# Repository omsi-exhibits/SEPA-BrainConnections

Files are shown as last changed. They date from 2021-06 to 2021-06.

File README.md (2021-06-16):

# OMSI's Brain Connections

## Next Steps
* update accelerometer code to use timers instead of delays
* update all the code to use timers instead of delays

## Other Todos
* consolodate notes
* write a good readme
* document High Level Design

## Known Bugs
none atm

# Flashing new firmware
The Itsybitsy32u4_5v is a litte finiky when it comes to flashing. The process that works most of the time for me is to double press the reset button
and then super quickly upload the code. Like within 300milliseconds or less. Maybe disabling serial.print()s would help? 

# Troubleshooting Tips
Removing and reinserting microcontroller is delicate and needs you to support the bottom of the mainboard with your hand.

## Fun Ideas
* Easter Egg Color pallette swap
* Sensor held on startup could change colors
* Handheld brain-connections game-thing

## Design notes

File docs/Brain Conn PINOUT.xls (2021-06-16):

Last updated: 11/30/20
LED Segment Names | SEGMENT LED COUNT | PINOUT FULL TABLE | Notes
node1LedCount | 24 | Digital out 7
node2LedCount | 24 | Digital out 7
node3LedCount | 24 | Digital out 7
node4LedCount | 24 | Digital out 7
node5LedCount | 24 | Digital out 7
node6LedCount | 24 | Digital out 7
node7LedCount | 24 | Digital out 7
conn1LedCount | 17 | Digital out 13
conn2LedCount | 8 | Digital out 13
conn3LedCount | 23 | Digital out 13
conn4LedCount | 23 | Digital out 13
conn5LedCount | 8 | Digital out 13
conn6LedCount | 17 | Digital out 13
conn7LedCount | 17 | Digital out 13
conn8LedCount | 10 | Digital out 13
conn9LedCount | 16 | Digital out 13
conn10LedCount | 21 | Digital out 13
conn11LedCount | 16 | Digital out 13
conn12LedCount | 16 | Digital out 13
orphan1LedCount | 15,5,3,5,15 | Digital out 5 | In code use the biggest orphan led count
orphan2LedCount | 11,12 | Digital out 5
orphan3LedCount | 7,10 | Digital out 5
orphans4LedCount | 19,7,2,7,19 | Digital out 5
orphans5LedCount | 10,7 | Digital out 5
orphans6LedCount | 11,11 no output wire | Digital out 5
sensor Status LEDs | 8 | Digital out 14
TILT_sensor | /ADXL343 accel | SPI wire buss
node1Sensor |  | ANALOG pin 0
node2Sensor |  | ANALOG pin 1
node3Sensor |  | ANALOG pin 2
node4Sensor |  | ANALOG pin 3
node5Sensor |  | ANALOG pin 4
node6Sensor |  | ANALOG pin 5
node7Sensor |  | ANALOG pin 6
Audio_1 | (IDLE sound - hold HIGH for looping) | DIGITAL out 12
Audio_2 | (Connection sound, edge triggered) | DIGITAL out 11
Audio_3 | (Node Sound, edge triggered) | DIGITAL out 10
Audio_4 | (Win Song, edge triggered) | DIGITAL out 9
Audio_5 | (Start song, edge triggered) | DIGITAL out 8

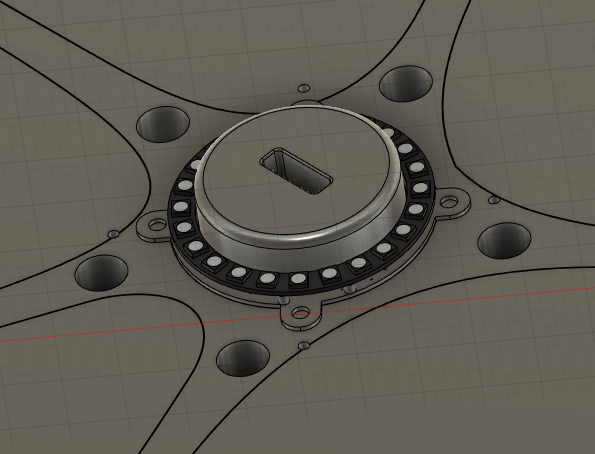
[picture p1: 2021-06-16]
3D/Brain Conn 3D Assets 7-22-20/LED Ring Location.png

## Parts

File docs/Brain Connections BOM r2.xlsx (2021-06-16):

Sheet: Summary Page
Estimate |  |  |  |  | DGTL.
Project Name | Brain Connections |  | Client | OMSI
Project # |  |  | Client Name | Caty Headskog
Date | 2020-03-23 |  | Launch Date | TBD
Production |  | PRICING | NOTES
Hardware |  | $802.88 | Please see BOM tab for detail. (Supplied by OMSI)
Total |  | $802.88

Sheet: BOM
Project Name | Brain Connections | Delivery Date | TBD
Project # | 0 | Ship Date | TBD
ITEM | DESCRIPTION | QTY | UNIT PRICE | SUBTOTAL | Notes
Opto Sensors | OPB732 | 7 | $4.04 | $28.28 | https://www.digikey.com/short/zjwwc4
Neopixel strip | 60/meter RGBW sk6812 (5050) (4 meter roll) | 2 | $107.80 | $215.60 | https://www.mouser.com/ProductDetail/Adafruit/2842
NeoPixel Rings | 24 pixels, RGBW | 7 | $19.95 | $139.65 | https://www.digikey.com/short/zjvqdr
3 axis accelerometer | adxl 343 | 1 | $5.95 | $5.95 | https://www.digikey.com/short/zjwwjd
Microcontroller | itsybitsy 32u4 5v 16mhz | 1 | $9.95 | $9.95 | https://www.digikey.com/short/zjwf45
12v power supply | 240w 115vac to 12vdc supply | 1 | $78.14 | $78.14 | https://www.digikey.com/short/zjwdpc
Dc - dc converter | 55w 12vdc to 5vdc converter | 3 | $16.41 | $49.23 | https://www.digikey.com/short/zjwd54
JST-SH with 3 leads extensions | 3 pin male + female set at 10 pair x 0.5 meter | 1 | $14.39 | $14.39 | https://www.amazon.com/RGBZONE-Extension-solderless-Connector-Symphony/dp/B06XSDZLPC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
JST-SH with 3 leads | 3 pin male + female set at 50 pair | 1 | $10.99 | $10.99 | https://www.amazon.com/HKBAYI-50Pair-50sets-Connector-WS2812B/dp/B00NBSH4CA
Phoenix connectors | TERM BLOCK PLUG 2POS STR 5.08MM | 14 | $3.20 | $44.80 | https://www.digikey.com/short/zjd0pv
Phoenix connectors | TERM BLOCK PLUG 3POS STR 5.08MM | 18 | $4.80 | $86.40 | https://www.digikey.com/short/zjd0zj
Phoenix connectors | TERM BLOCK PLUG 4POS STR 5.08MM | 2 | $6.44 | $12.88 | https://www.digikey.com/short/zjd0z2
Phoenix connectors | TERM BLOCK HDR 2POS 90DEG 5.08MM | 14 | $0.64 | $8.96 | https://www.digikey.com/short/zjd078
Phoenix connectors | TERM BLOCK HDR 3POS 90DEG 5.08MM | 18 | $1.03 | $18.54 | https://www.digikey.com/short/zjd032
Phoenix connectors | TERM BLOCK HDR 4POS 90DEG 5.08MM | 2 | $1.40 | $2.80 | https://www.digikey.com/short/zjd03d
Phoenix connectors | TERM BLK 6P SIDE ENT 5.08MM PCB | 1 | $3.16 | $3.16 | https://www.digikey.com/short/zjd00v
Panasonic Capacitors | CAP ALUM 1000UF 20% 25V RADIAL | 4 | $0.79 | $3.16 | https://www.digikey.com/short/zjv8j5
100 Ohm 1/4 watt resistor | RES 100 OHM 1/4W 5% AXIAL | 7 | $0.10 | $0.70 | https://www.digikey.com/short/zjv8b2
330 Ohm 1/4 watt resistor | RES 330 OHM 1/4W 5% AXIAL | 4 | $0.10 | $0.40 | https://www.digikey.com/short/zjv8h1
1k Ohm 1/4 watt resistor | RES 1K OHM 1/4W 5% AXIAL | 7 | $0.10 | $0.70 | https://www.digikey.com/short/zjv8b4
aluminum track | 0.69in w x 0.28in high OD (0.48" wide ID) | 1 | $68.20 | $68.20 | https://www.amazon.com/hunhun-Aluminum-Mounting-Installations-Installation/dp/B07F923CXW
audio interface | Wav Trigger WIG-13660 | 1 | $0.00 | $0.00 | Provided by OMSI
amplifier |  | 1 | $0.00 | $0.00 | Provided by OMSI
 |  |  |  | $802.88

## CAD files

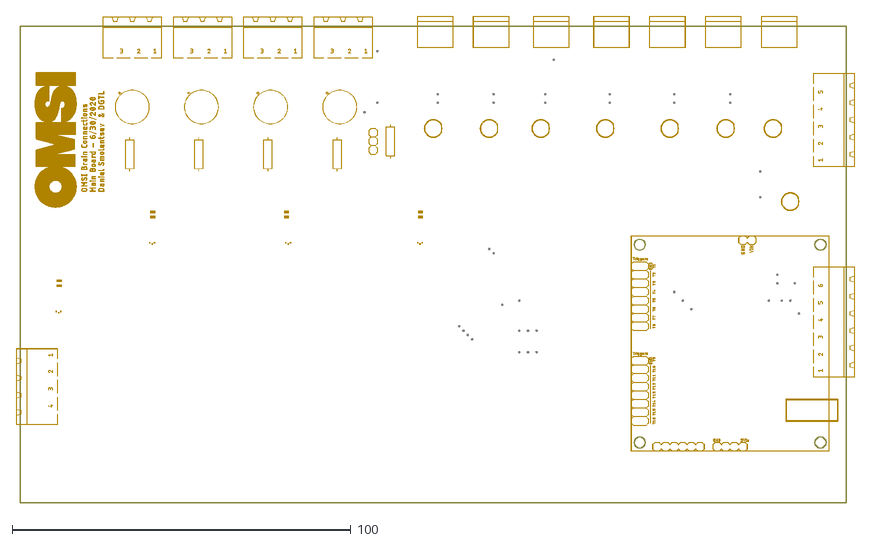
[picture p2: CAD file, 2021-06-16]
3D/Brain Conn 3D Assets 7-22-20/Mainboard - OMSI_TABLE_R12_v4 - Simple.dxf
247.5 x 143.6

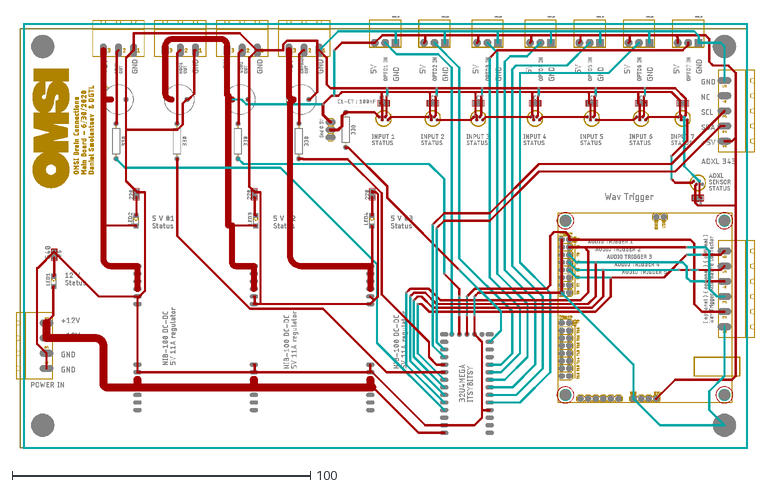
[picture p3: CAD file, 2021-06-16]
3D/Brain Conn 3D Assets 7-22-20/alt files/Mainboard - OMSI_TABLE_R12_v4 - Complex.dxf
247.5 x 145.0

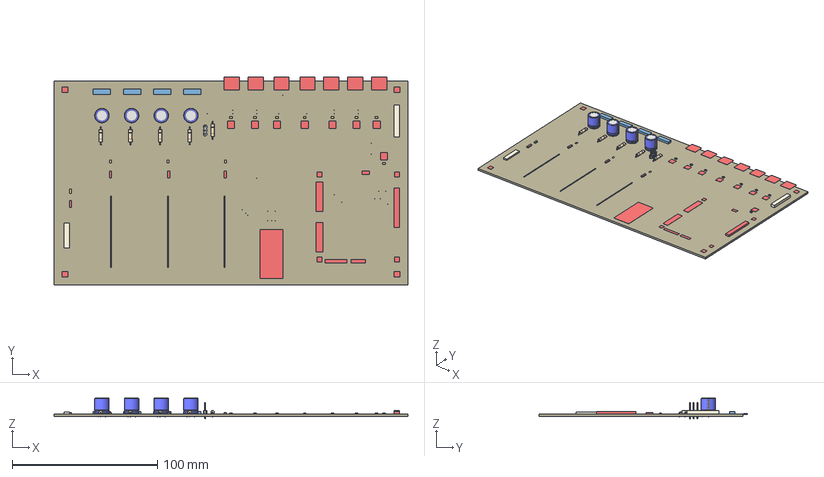
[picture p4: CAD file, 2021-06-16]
3D/Brain Conn 3D Assets 7-22-20/alt files/Mainboard - OMSI_TABLE_R12_v4.step
243.8 x 143.5 x 14.3 mm
Board
MSTBA3 x 4
CHIPLED_1206 x 4
MEANWELL_NID100 x 3
ITSYBITSY_32U4
C-POL-US_RADIAL-11MM-DIA x 4
MSTBA4
MSTBA5
STANDOFF_ELECTRICAL5-32 x 4
1X06
STAND-OFF x 4
M08X2 x 2
1X04
M02PTH
CONN_03 x 7
APA106-F5 x 8
100nF x 8
MSTBA6
1X03

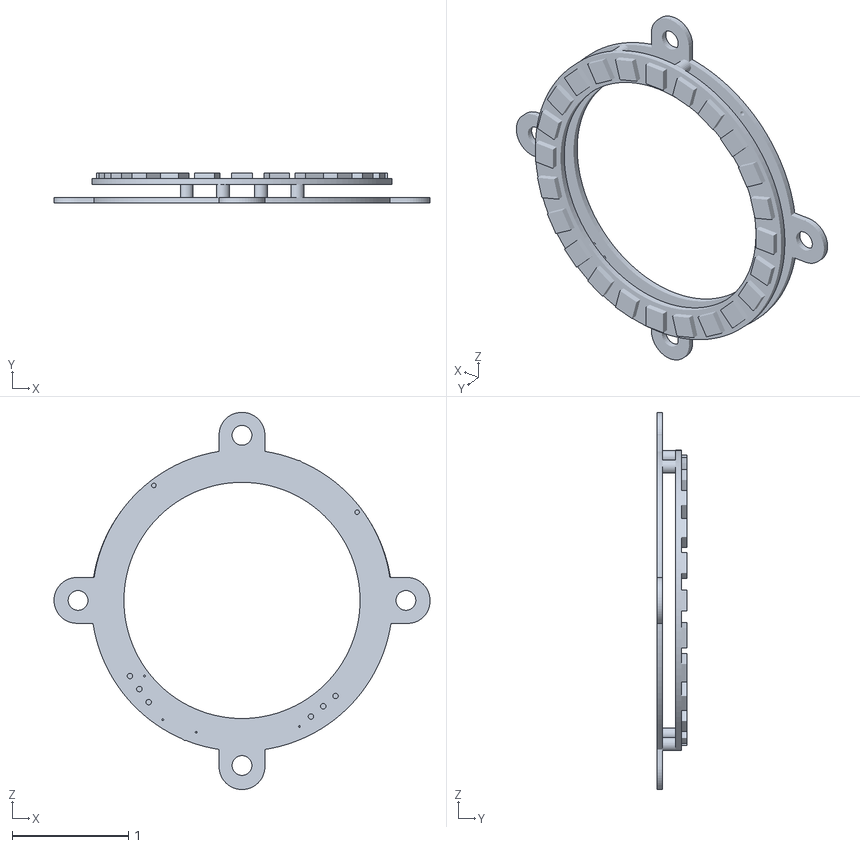
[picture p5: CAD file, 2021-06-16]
3D/Brain Conn 3D Assets 7-22-20/LED Ring - LED ASSEMBLY.stl
3.23 x 0.26 x 3.24

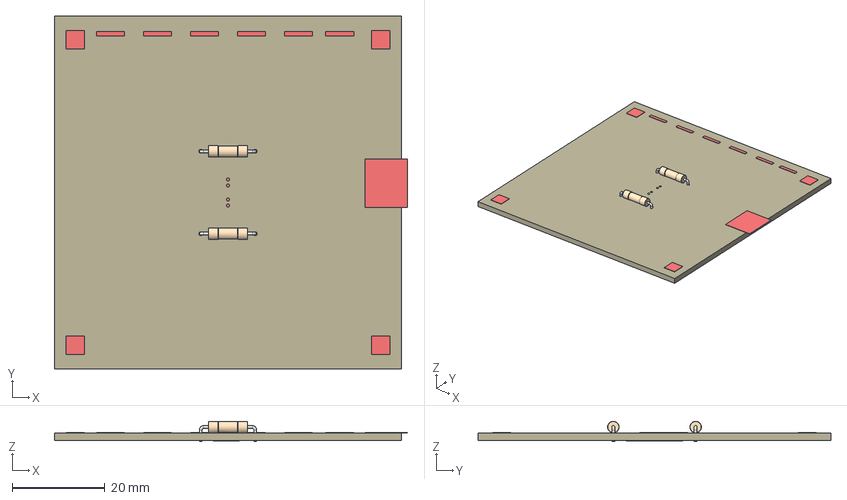
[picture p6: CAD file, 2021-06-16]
3D/Brain Conn 3D Assets 7-22-20/alt files/Sensorboard - Ring_opto_interface_v3.step
76.2 x 76.2 x 4.42 mm
Board
1X03-CLEANBIG x 6
10k x 2
STANDOFF_ELECTRICAL5-32 x 4
OPB732
CONN_03

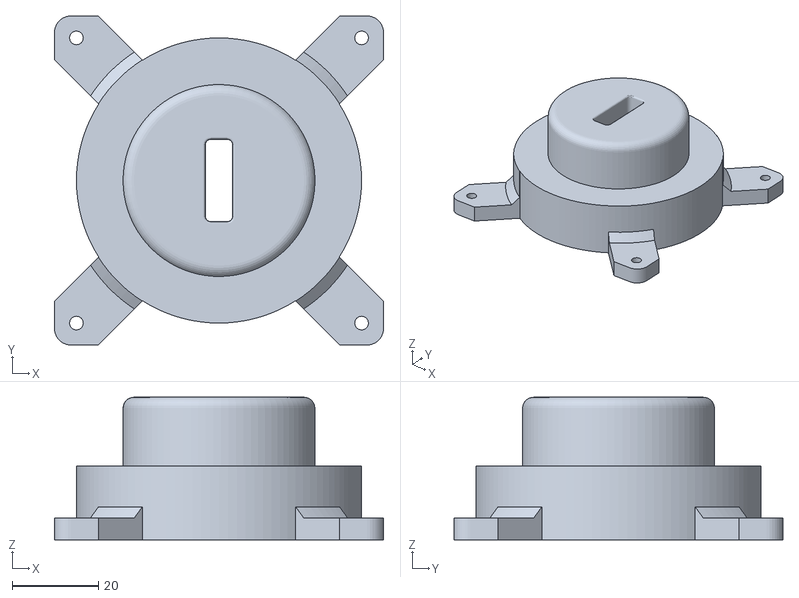
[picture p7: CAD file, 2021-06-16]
3D/Spacer 4 Holes.stl
76.2 x 76.2 x 33.0

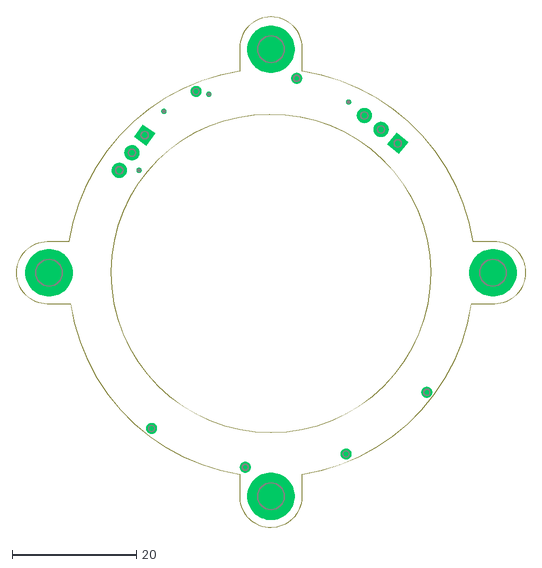
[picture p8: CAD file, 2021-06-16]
pcb/eagle/neopixel_ring_24_holder/Adafruit NeoPixel Ring 24 B - Holder 3 Outline.dxf
82.1 x 82.3

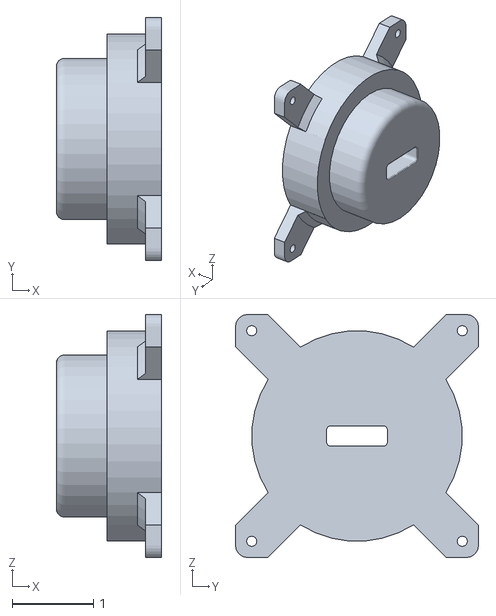
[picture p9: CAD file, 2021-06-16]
3D/3D Spacer v2.obj
1.30 x 3.00 x 3.00

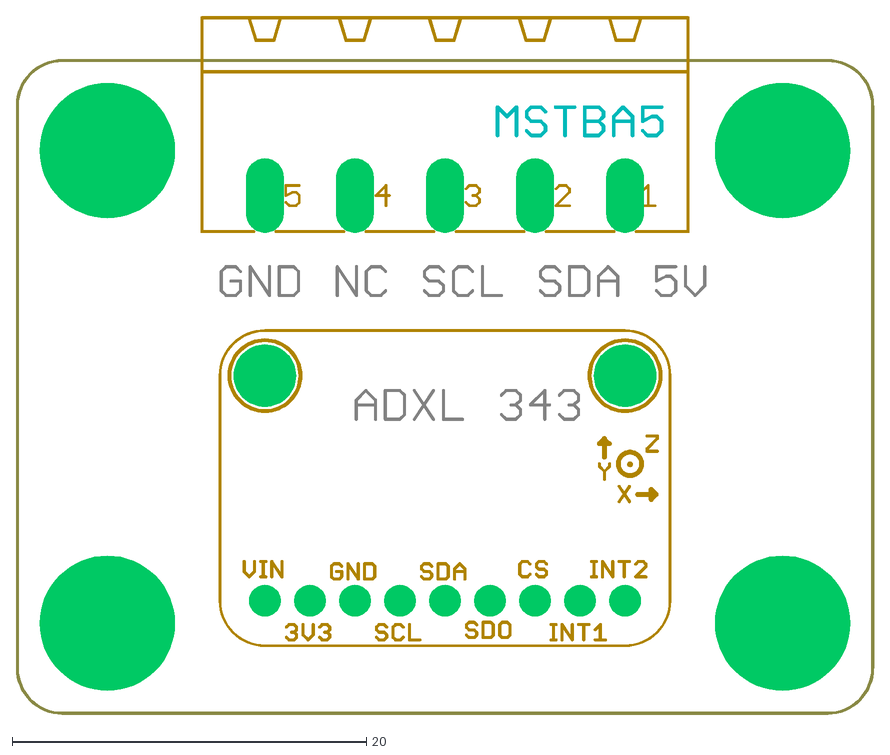
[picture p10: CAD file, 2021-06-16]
pcb/eagle/pcb updates redesign/ADXL Breakout Board V1.dxf
48.4 x 39.4

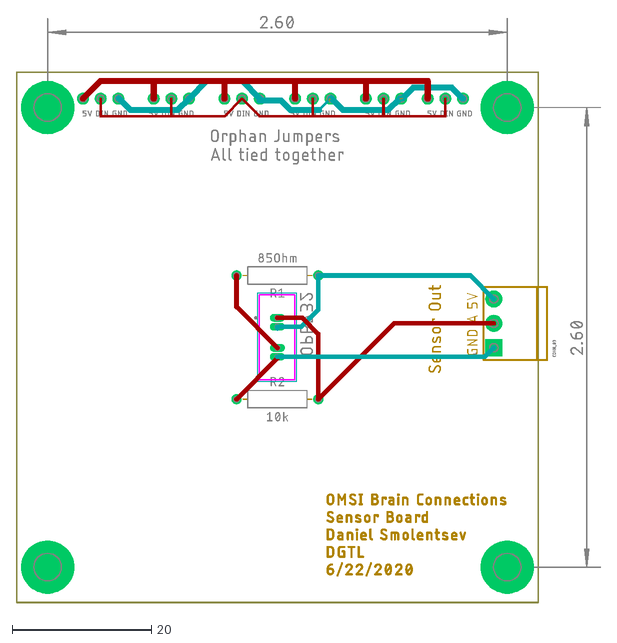
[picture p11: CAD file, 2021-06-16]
3D/Brain Conn 3D Assets 7-22-20/Sensor board - Ring_opto_interface_v3.dxf
84.0 x 84.3

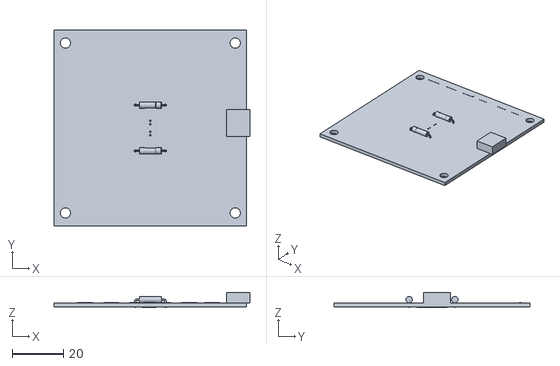
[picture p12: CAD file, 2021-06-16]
3D/Brain Conn 3D Assets 7-22-20/Sensor Board - Ring_opto_interface_v3 v2.stl
76.2 x 76.2 x 6.02

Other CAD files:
3D/Brain Conn 3D Assets 7-22-20/MainBoard - OMSI_TABLE_R12_v4.stl
3D/3D Spacer v2.dxf
3D/3D Spacer v2.f3d
3D/Brain Conn 3D Assets 7-22-20/Accelerometer - ADXL Breakout Board V1 v1.stl
3D/OMSI_TABLE_STATLEDS.f3z
3D/Ring_OPTO_2V5.f3z
3D/node spacer v2.f3d

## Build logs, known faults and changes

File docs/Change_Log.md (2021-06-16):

# Brain Connections Change log

5/14/20 Expanded the number of nodes, connections, orphans
Removed Words
5/20/20
mcu is running out of RAM. 
5/21/20
To reduce RAM usage I replaced the Adafruit Accelerometer library with sparkfun one.
There is still not enough space in SRAM. Converted the Serial Prints
to use F() to wrap strings to make it save into program memory instead of RAM.
Those two changes yielded enough space in SRAM.
5/21/20
Updated the Opto input pins to match the PCBs out of order pins.
5/26/20
Fixing connection segment bugs.
Added a Serial input from computer to trigger Nodes.
6/3/20
Added Individual OPTOtriggerValue for each OPTO
6/24/20 update
Wav trigger audio inputs set to these pins
const int Audio_1 = 8; // Idle Song - hold level high to loop
const int Audio_2 = 9; // Connection on 10 - edge triggered
const int Audio_3 = 10; // Node sound on 9 - edge triggered
const int Audio_4 = 11; // Win sound on 8 - edge triggered
const int Audio_5 = 12; // Start Song on 11 - edge triggered
7/15/20
Modified led type for sensorsout to neopixel GRB
Updated Sensor pins
Updated Audio out pins
11-23-20
Updated sensor trigger values to 350 on line#s105
4-14-21
Fixed Audio trigger pins to play win sound correctly
6-15-21
Updated accelZTriggerValue from 20 to 11 for a more responsive trigger
Fixed Node7 not dimming

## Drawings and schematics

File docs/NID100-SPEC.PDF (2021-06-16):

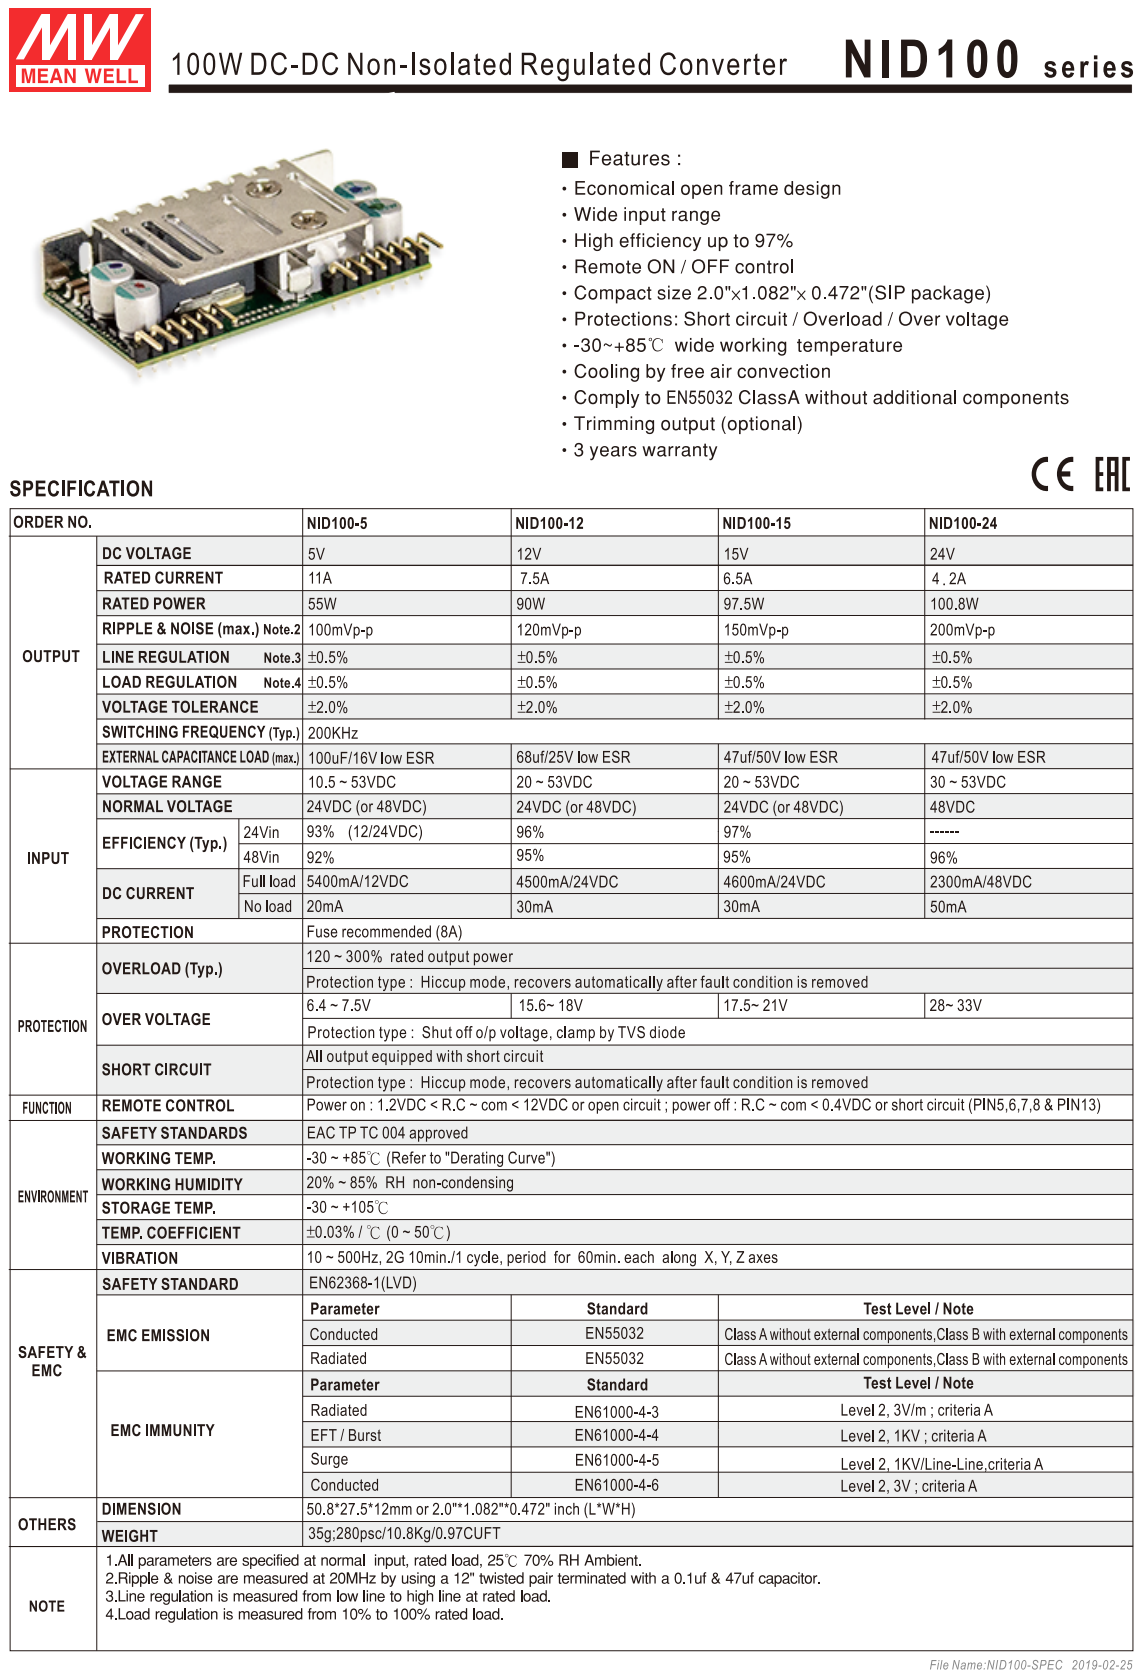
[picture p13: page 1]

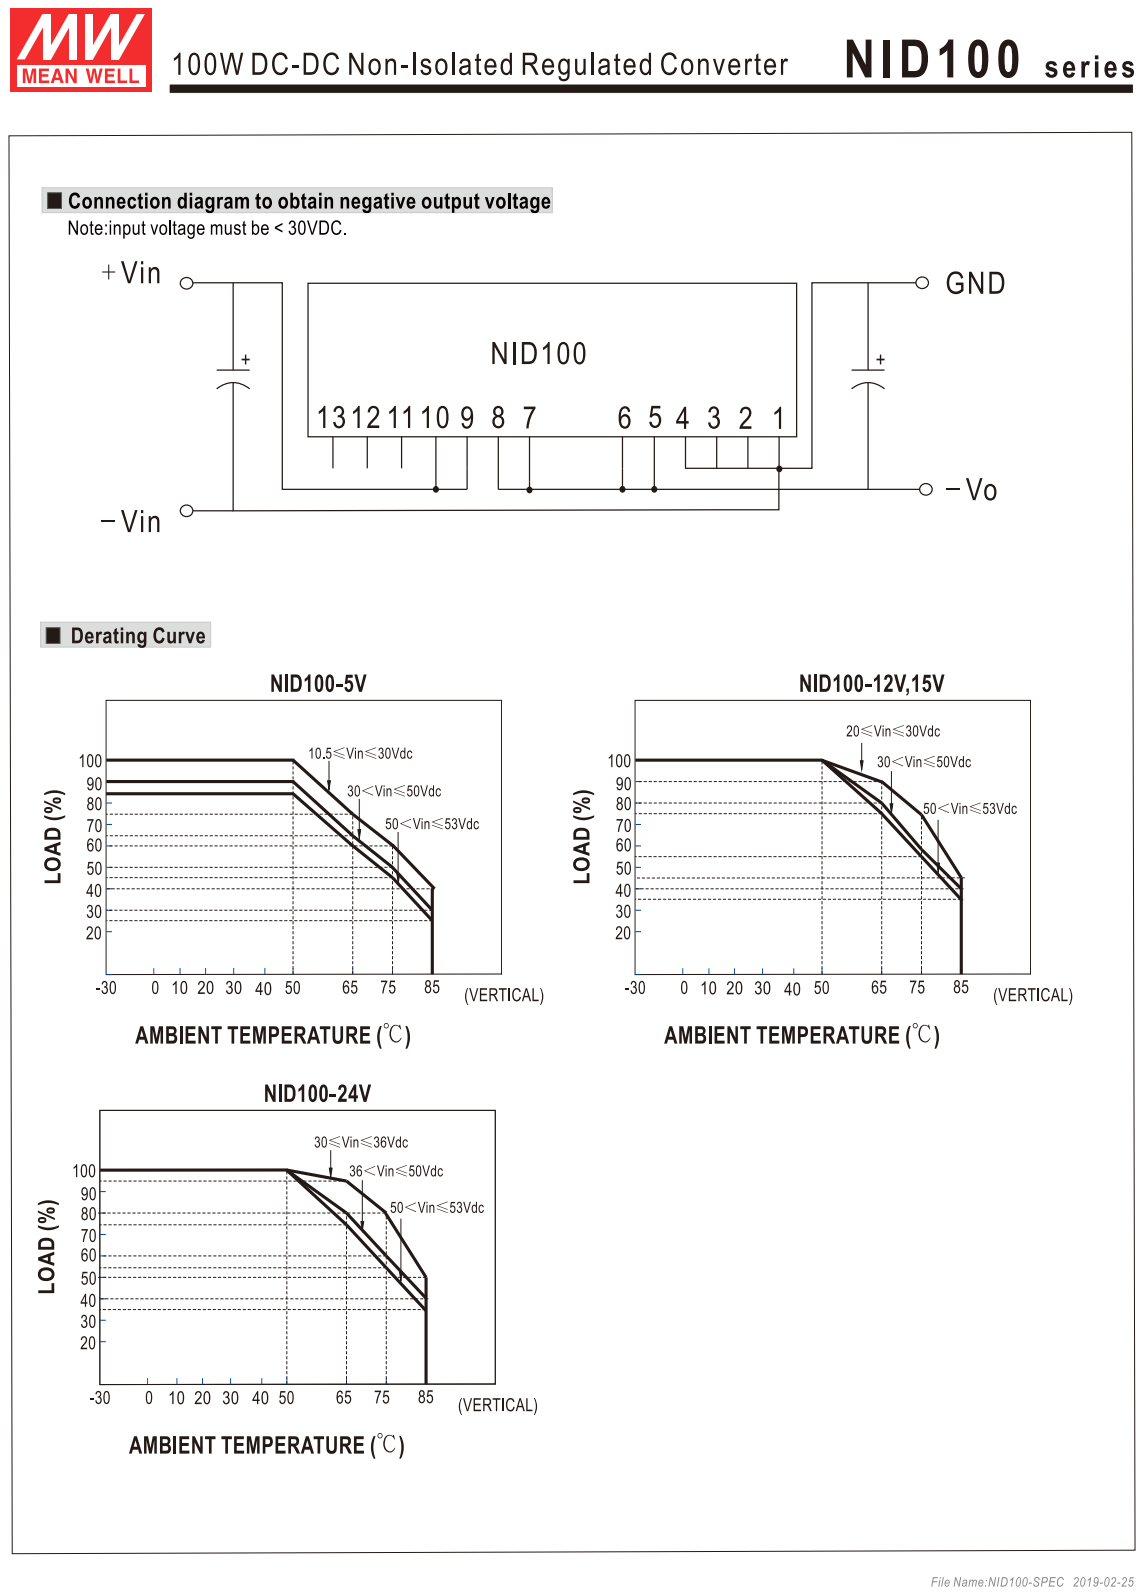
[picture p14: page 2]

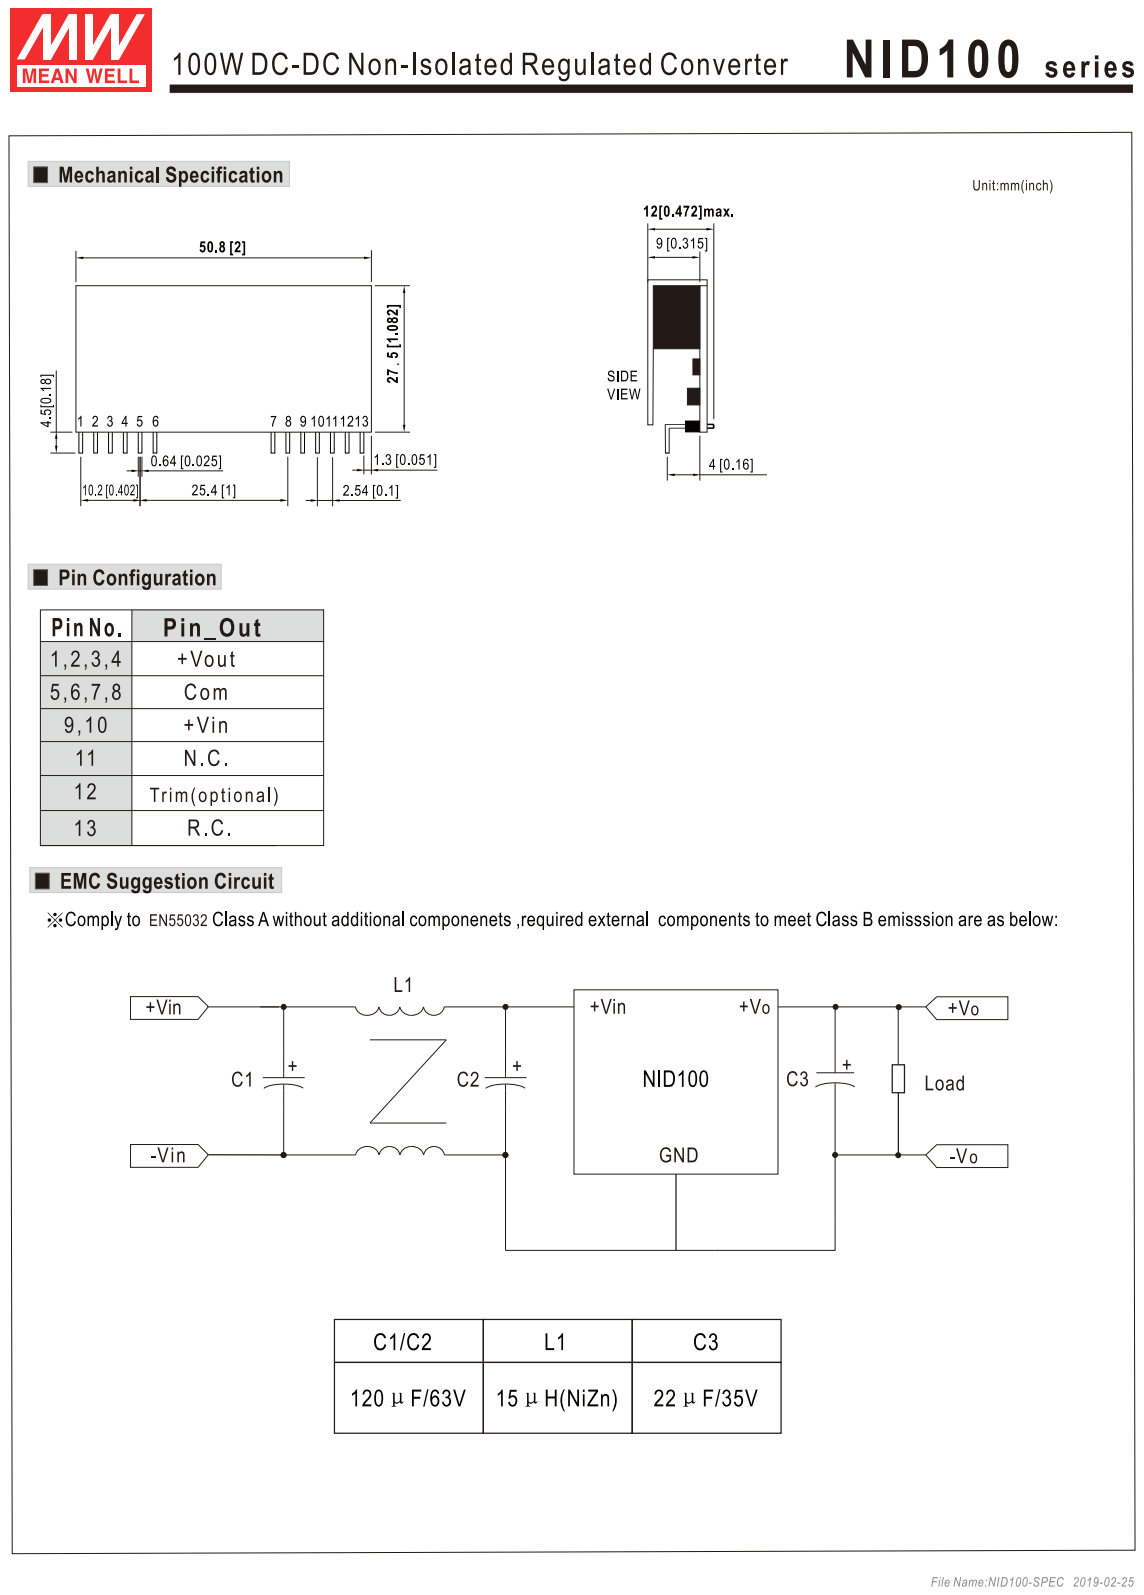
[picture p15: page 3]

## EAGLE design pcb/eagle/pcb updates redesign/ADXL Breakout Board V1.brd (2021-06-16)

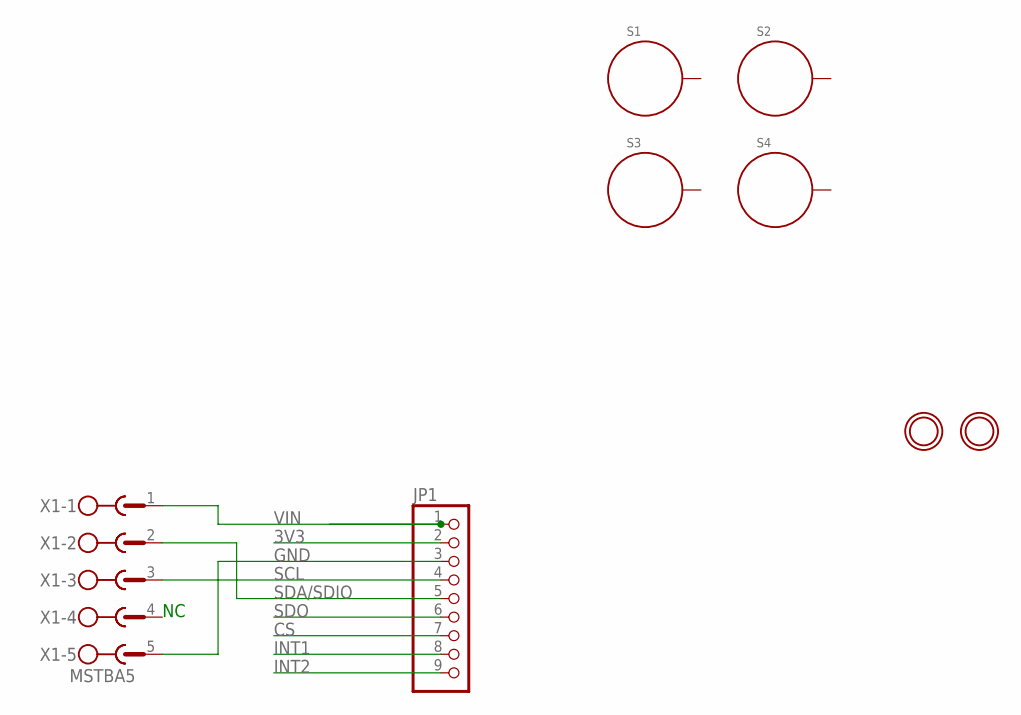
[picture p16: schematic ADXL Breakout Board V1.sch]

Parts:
JP1: HEADER-1X970MIL; 1X09_ROUND_70
S1, S2, S3, S4: STANDOFF_ELECTRICAL5-32; STANDOFF_ELECTRICAL_5_32
U$4, U$6: MOUNTINGHOLE2.5; MOUNTINGHOLE_2.5_PLATED
X1: MSTBA5

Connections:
3V3: JP1.2
CS: JP1.7
GND: JP1.3, X1.5
INT1: JP1.8
INT2: JP1.9
SCL: JP1.4, X1.3
SDA/SDIO: JP1.5, X1.2
SDO: JP1.6
VIN: JP1.1, X1.1

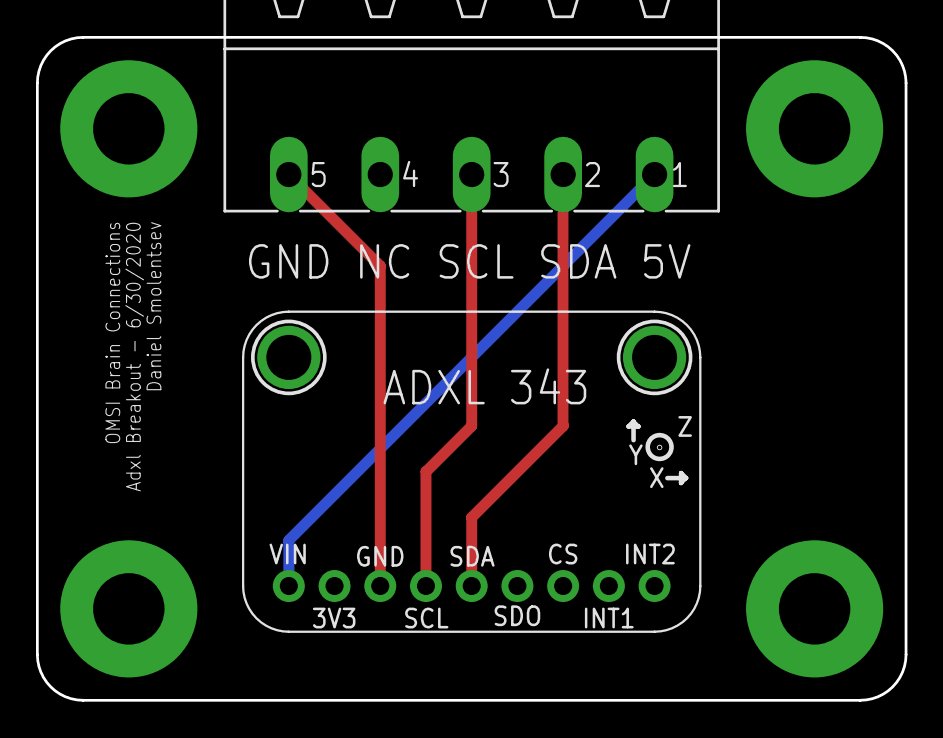
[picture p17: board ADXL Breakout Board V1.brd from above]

Board: 2 copper layers, 48.3 x 36.8 mm, 8 parts (0 on the bottom side), 4 nets.

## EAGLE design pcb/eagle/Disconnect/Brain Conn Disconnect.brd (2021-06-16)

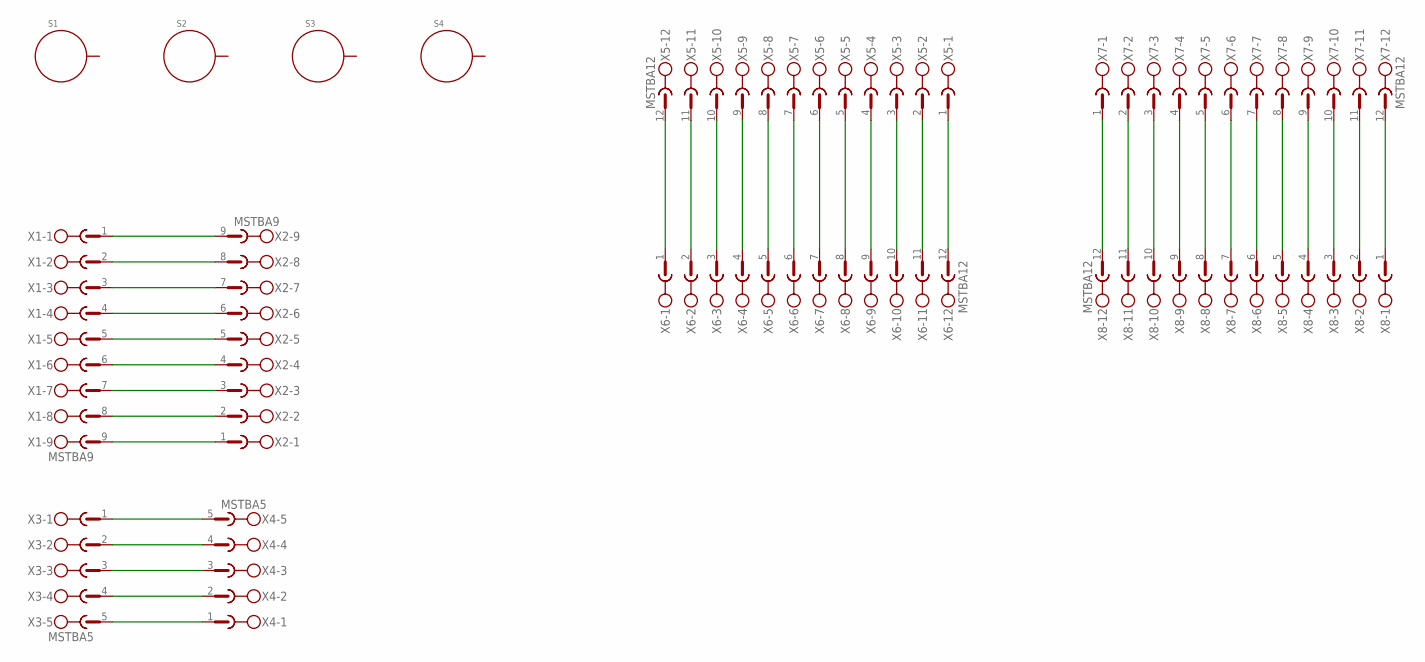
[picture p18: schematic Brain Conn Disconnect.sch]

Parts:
S1, S2, S3, S4: STANDOFF_ELECTRICAL144; STANDOFF_ELECTRICAL_144MILL_NORMAL_SCREW
X1, X2: MSTBA9
X3, X4: MSTBA5
X5, X6, X7, X8: MSTBA12

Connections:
unnamed: X3.1, X4.5
unnamed: X3.2, X4.4
unnamed: X3.3, X4.3
unnamed: X3.4, X4.2
unnamed: X3.5, X4.1
unnamed: X1.1, X2.9
unnamed: X1.2, X2.8
unnamed: X1.3, X2.7
unnamed: X1.4, X2.6
unnamed: X1.5, X2.5
unnamed: X1.6, X2.4
unnamed: X1.7, X2.3
unnamed: X1.8, X2.2
unnamed: X1.9, X2.1
unnamed: X5.12, X6.1
unnamed: X5.11, X6.2
unnamed: X5.10, X6.3
unnamed: X5.9, X6.4
unnamed: X5.8, X6.5
unnamed: X5.7, X6.6
unnamed: X5.6, X6.7
unnamed: X5.5, X6.8
unnamed: X5.4, X6.9
unnamed: X5.3, X6.10
unnamed: X5.2, X6.11
unnamed: X5.1, X6.12
unnamed: X7.1, X8.12
unnamed: X7.2, X8.11
unnamed: X7.3, X8.10
unnamed: X7.4, X8.9
unnamed: X7.5, X8.8
unnamed: X7.6, X8.7
unnamed: X7.7, X8.6
unnamed: X7.8, X8.5
unnamed: X7.9, X8.4
unnamed: X7.10, X8.3
unnamed: X7.11, X8.2
unnamed: X7.12, X8.1

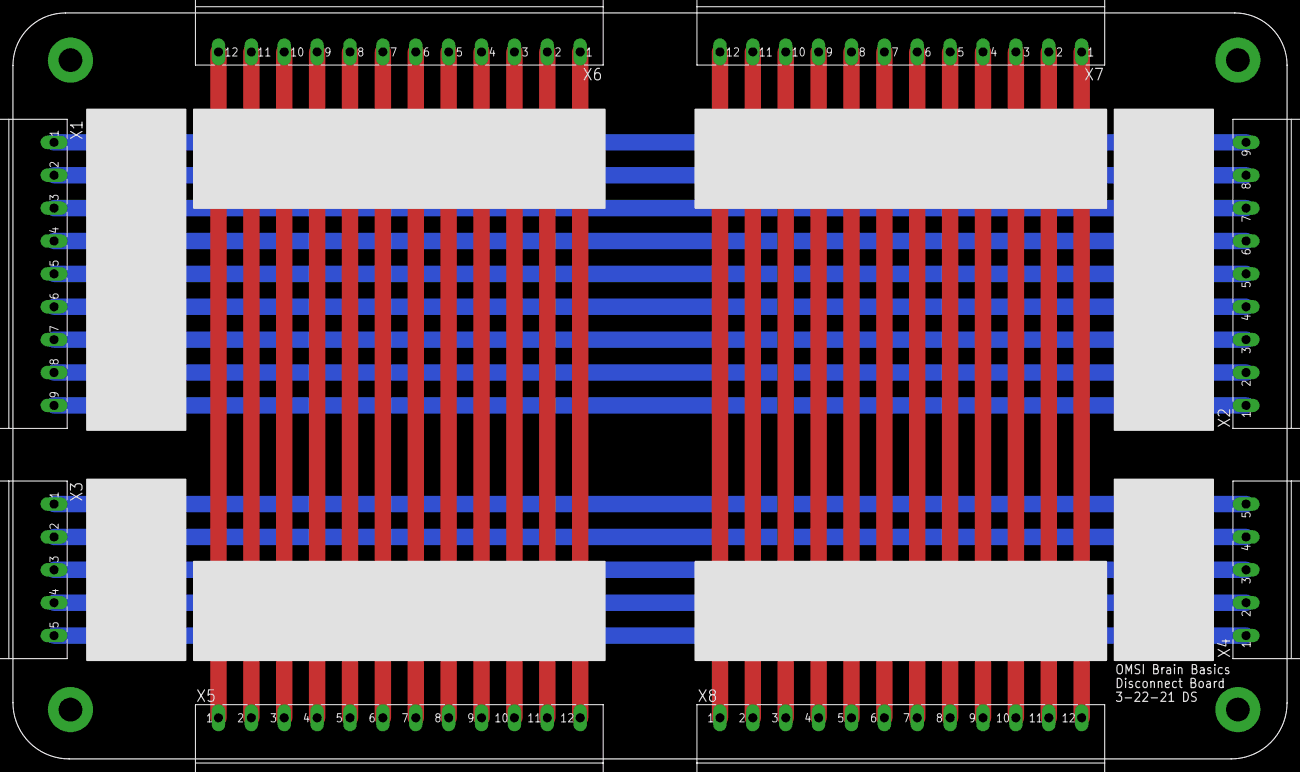
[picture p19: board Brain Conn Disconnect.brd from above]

Board: 2 copper layers, 196.8 x 115.2 mm, 12 parts (0 on the bottom side), 38 nets.

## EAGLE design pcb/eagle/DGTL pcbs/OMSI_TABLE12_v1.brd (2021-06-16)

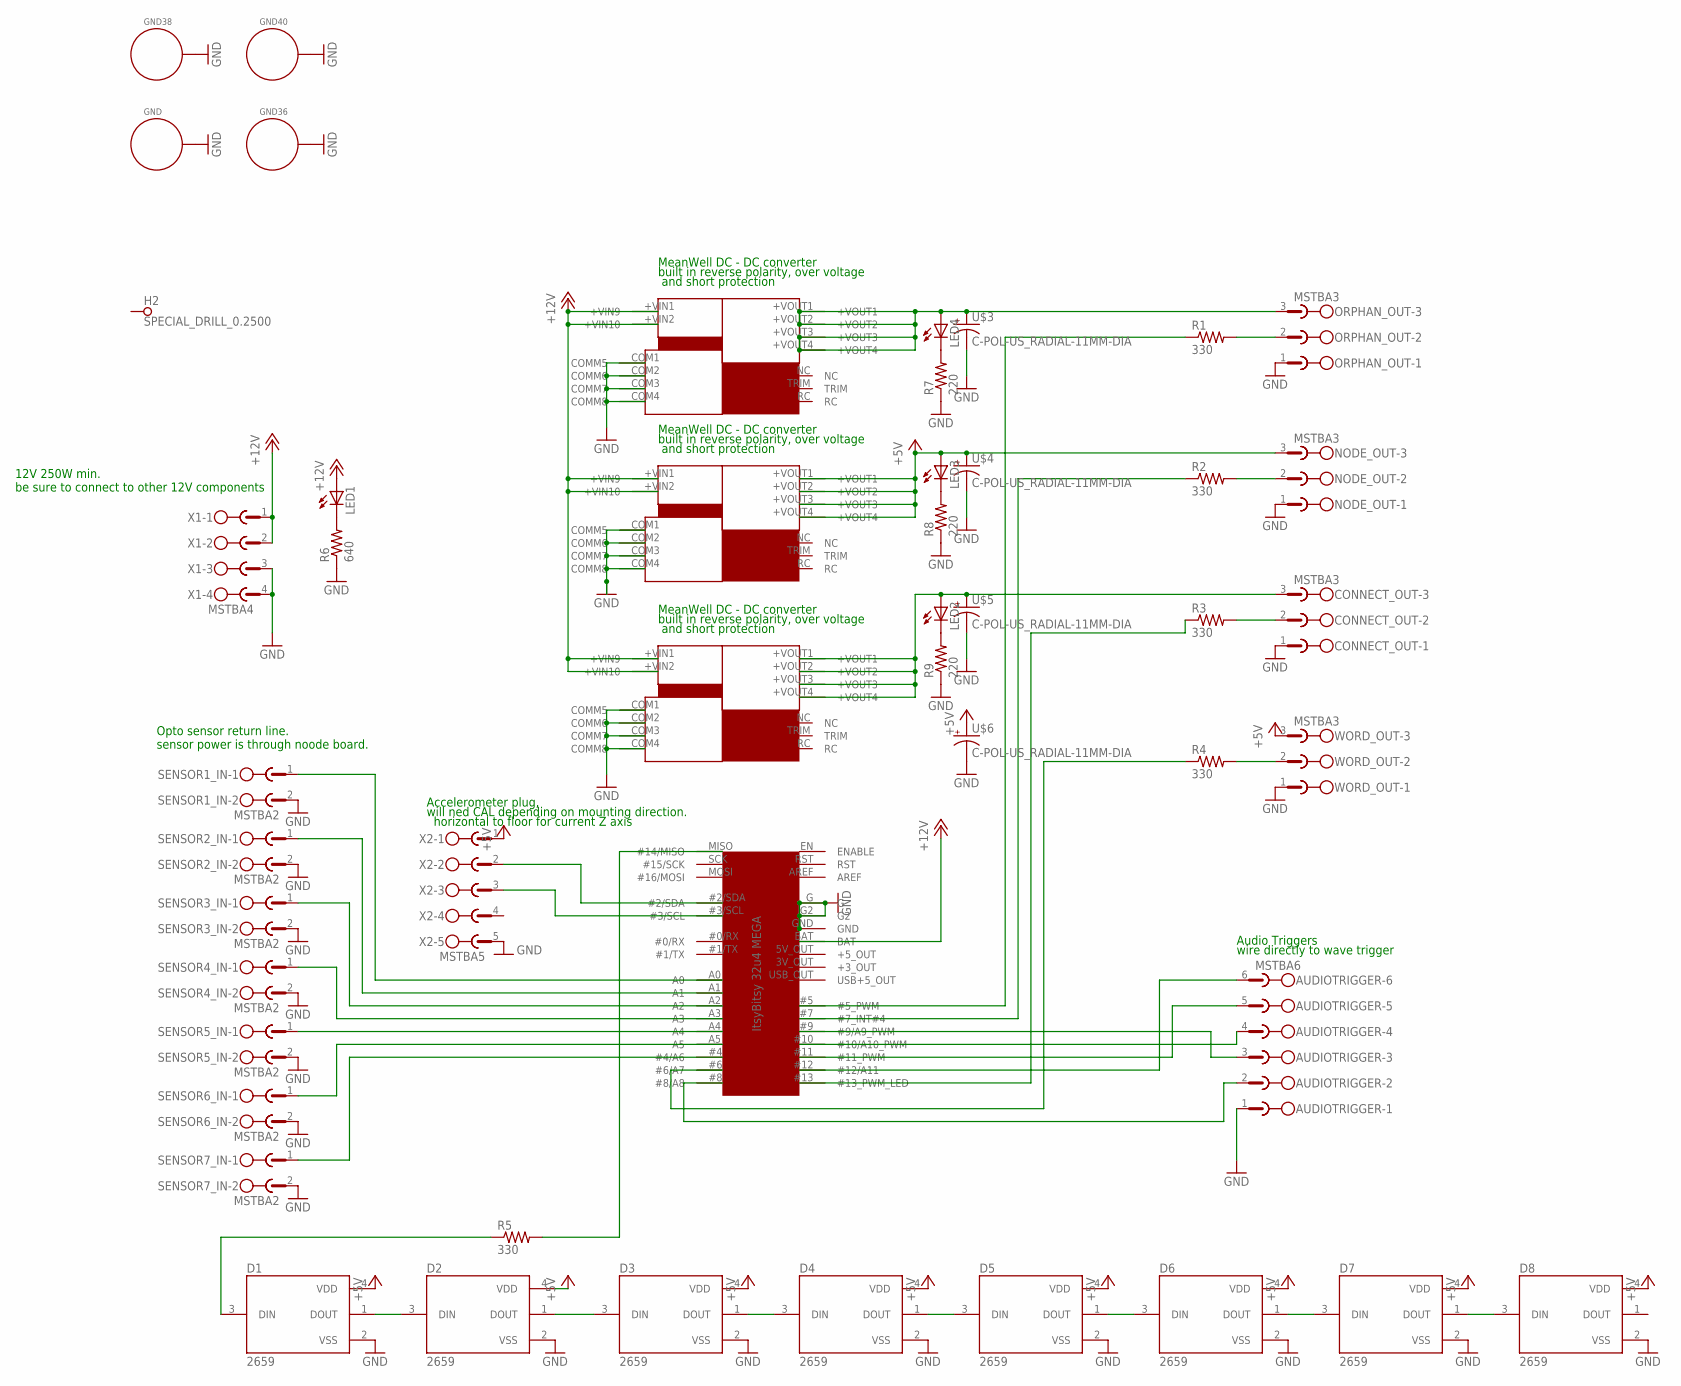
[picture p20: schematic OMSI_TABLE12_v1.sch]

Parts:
AUDIOTRIGGER: MSTBA6
CONNECT_OUT: MSTBA3
D1, D2, D3, D4, D5, D6, D7, D8: 2659
GND, GND36, GND38, GND40: STANDOFF_ELECTRICAL5-32; STANDOFF_ELECTRICAL_5_32
H2: SPECIAL_DRILL_0.2500; PAD_0.2500
LED1, LED2, LED3, LED4: LEDCHIPLED_1206; CHIPLED_1206
MEANWELL_NID100_1, MEANWELL_NID100_2, MEANWELL_NID100_3: MEANWELL_NID100
NODE_OUT: MSTBA3
ORPHAN_OUT: MSTBA3
R1, R2, R3, R4, R5: 330; RESAD1176W63L850D250B
R6: 640; R0805
R7, R8, R9: 220; R0805
SENSOR1_IN, SENSOR2_IN, SENSOR3_IN, SENSOR4_IN, SENSOR5_IN, SENSOR6_IN, SENSOR7_IN: MSTBA2
U$1: ITSYBITSY_32U4
U$3, U$4, U$5, U$6: C-POL-US_RADIAL-11MM-DIA; CAPPRD508W65D1000H1100B
WORD_OUT: MSTBA3
X1: MSTBA4
X2: MSTBA5

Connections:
+3_OUT: U$1.3V_OUT (+3_OUT)
+5V: D1.4 (VDD), D2.4 (VDD), D3.4 (VDD), D4.4 (VDD), D5.4 (VDD), D6.4 (VDD), D7.4 (VDD), D8.4 (VDD), LED3.A, MEANWELL_NID100_3.+VOUT1, MEANWELL_NID100_3.+VOUT2, MEANWELL_NID100_3.+VOUT3, MEANWELL_NID100_3.+VOUT4, NODE_OUT.3, U$4.1 (+), U$6.1 (+), WORD_OUT.3, X2.1
+5_OUT: U$1.5V_OUT (+5_OUT)
+12V: LED1.A, MEANWELL_NID100_1.+VIN1 (+VIN9), MEANWELL_NID100_1.+VIN2 (+VIN10), MEANWELL_NID100_2.+VIN1 (+VIN9), MEANWELL_NID100_2.+VIN2 (+VIN10), MEANWELL_NID100_3.+VIN1 (+VIN9), MEANWELL_NID100_3.+VIN2 (+VIN10), U$1.BAT, X1.1, X1.2
AREF: U$1.AREF
GND: AUDIOTRIGGER.1, CONNECT_OUT.1, D1.2 (VSS), D2.2 (VSS), D3.2 (VSS), D4.2 (VSS), D5.2 (VSS), D6.2 (VSS), D7.2 (VSS), D8.2 (VSS), GND.P1, GND36.P1, GND38.P1, GND40.P1, MEANWELL_NID100_1.COM1 (COMM5), MEANWELL_NID100_1.COM2 (COMM6), MEANWELL_NID100_1.COM3 (COMM7), MEANWELL_NID100_1.COM4 (COMM8), MEANWELL_NID100_2.COM1 (COMM5), MEANWELL_NID100_2.COM2 (COMM6), MEANWELL_NID100_2.COM3 (COMM7), MEANWELL_NID100_2.COM4 (COMM8), MEANWELL_NID100_3.COM1 (COMM5), MEANWELL_NID100_3.COM2 (COMM6), MEANWELL_NID100_3.COM3 (COMM7), MEANWELL_NID100_3.COM4 (COMM8), NODE_OUT.1, ORPHAN_OUT.1, R6.1, R7.1, R8.1, R9.1, SENSOR1_IN.2, SENSOR2_IN.2, SENSOR3_IN.2, SENSOR4_IN.2, SENSOR5_IN.2, SENSOR6_IN.2, SENSOR7_IN.2, U$1.G, U$1.G2, U$1.GND, U$3.2 (-), U$4.2 (-), U$5.2 (-), U$6.2 (-), WORD_OUT.1, X1.3, X1.4, X2.5
unnamed: LED4.A, MEANWELL_NID100_2.+VOUT1, MEANWELL_NID100_2.+VOUT2, MEANWELL_NID100_2.+VOUT3, MEANWELL_NID100_2.+VOUT4, ORPHAN_OUT.3, U$3.1 (+)
unnamed: U$1.#2/SDA, X2.2
unnamed: U$1.#3/SCL, X2.3
unnamed: SENSOR1_IN.1, U$1.A0
unnamed: SENSOR2_IN.1, U$1.A1
unnamed: SENSOR3_IN.1, U$1.A2
unnamed: CONNECT_OUT.3, LED2.A, MEANWELL_NID100_1.+VOUT1, MEANWELL_NID100_1.+VOUT2, MEANWELL_NID100_1.+VOUT3, MEANWELL_NID100_1.+VOUT4, U$5.1 (+)
unnamed: SENSOR4_IN.1, U$1.A3
unnamed: ORPHAN_OUT.2, R1.2
unnamed: R1.1, U$1.#5 (#5_PWM)
unnamed: NODE_OUT.2, R2.2
unnamed: SENSOR5_IN.1, U$1.A4
unnamed: SENSOR6_IN.1, U$1.A5
unnamed: SENSOR7_IN.1, U$1.#4 (#4/A6)
unnamed: R2.1, U$1.#7 (#7_INT#4)
unnamed: CONNECT_OUT.2, R3.2
unnamed: R3.1, U$1.#13 (#13_PWM_LED)
unnamed: R4.2, WORD_OUT.2
unnamed: R4.1, U$1.#6 (#6/A7)
unnamed: AUDIOTRIGGER.6, U$1.#12 (#12/A11)
unnamed: AUDIOTRIGGER.5, U$1.#11 (#11_PWM)
unnamed: R5.2, U$1.MISO (#14/MISO)
unnamed: AUDIOTRIGGER.4, U$1.#10 (#10/A10_PWM)
unnamed: AUDIOTRIGGER.3, U$1.#9 (#9/A9_PWM)
unnamed: AUDIOTRIGGER.2, U$1.#8 (#8/A8)
unnamed: D1.1 (DOUT), D2.3 (DIN)
unnamed: D2.1 (DOUT), D3.3 (DIN)
unnamed: D3.1 (DOUT), D4.3 (DIN)
unnamed: D4.1 (DOUT), D5.3 (DIN)
unnamed: D5.1 (DOUT), D6.3 (DIN)
unnamed: D6.1 (DOUT), D7.3 (DIN)
unnamed: D7.1 (DOUT), D8.3 (DIN)
unnamed: D1.3 (DIN), R5.1
unnamed: LED1.C, R6.2
unnamed: LED4.C, R7.2
unnamed: LED3.C, R8.2
unnamed: LED2.C, R9.2
RST: U$1.RST
USB+5_OUT: U$1.USB_OUT (USB+5_OUT)

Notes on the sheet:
12V 250W min. be sure to connect to other 12V components
Opto sensor return line. sensor power is through noode board.
Accelerometer plug, will ned CAL depending on mounting direction. horizontal to floor for current Z axis
MeanWell DC - DC converter built in reverse polarity, over voltage and short protection
Audio Triggers wire directly to wave trigger

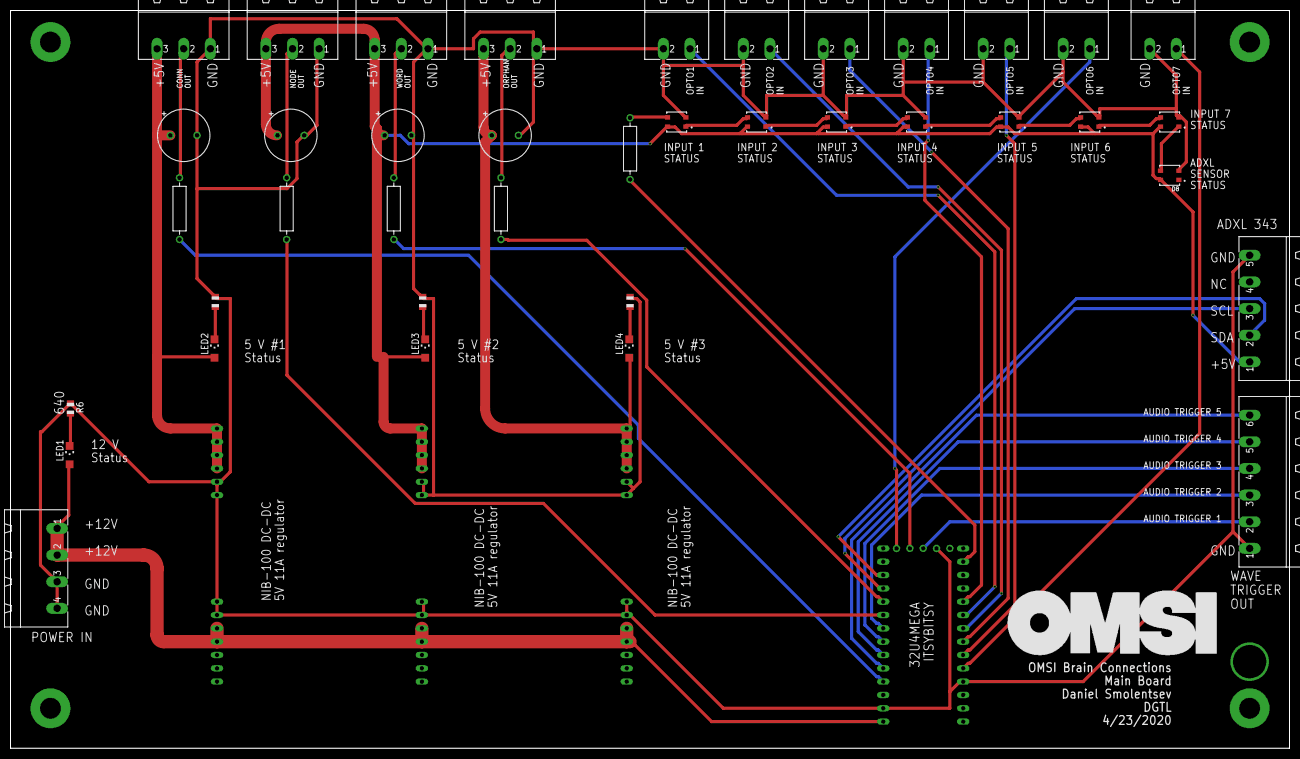
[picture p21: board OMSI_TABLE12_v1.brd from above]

Board: 2 copper layers, 243.8 x 140.6 mm, 48 parts (0 on the bottom side), 40 nets.

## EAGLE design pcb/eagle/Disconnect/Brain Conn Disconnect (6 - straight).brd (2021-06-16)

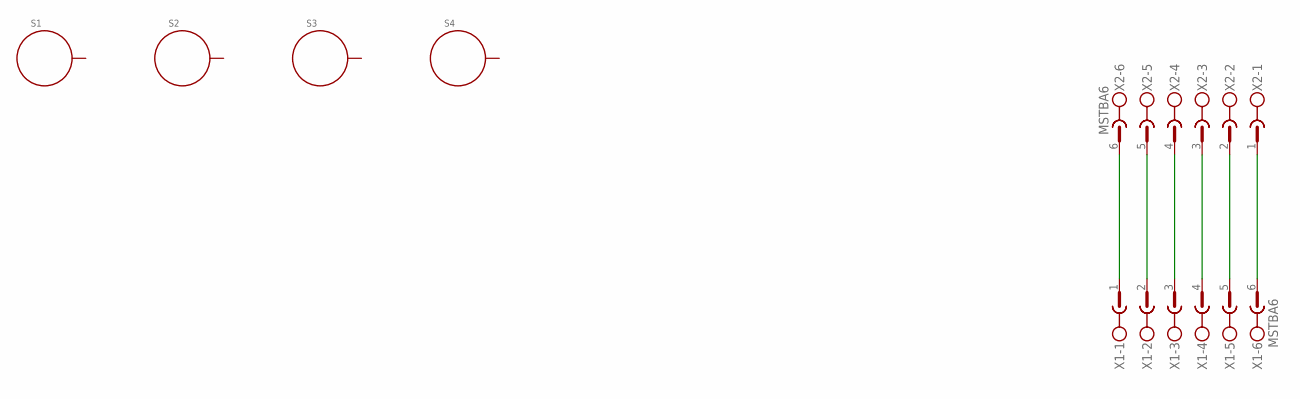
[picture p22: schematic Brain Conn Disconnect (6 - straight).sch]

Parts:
S1, S2, S3, S4: STANDOFF_ELECTRICAL144; STANDOFF_ELECTRICAL_144MILL_NORMAL_SCREW
X1, X2: MSTBA6

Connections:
unnamed: X1.1, X2.6
unnamed: X1.2, X2.5
unnamed: X1.3, X2.4
unnamed: X1.4, X2.3
unnamed: X1.5, X2.2
unnamed: X1.6, X2.1

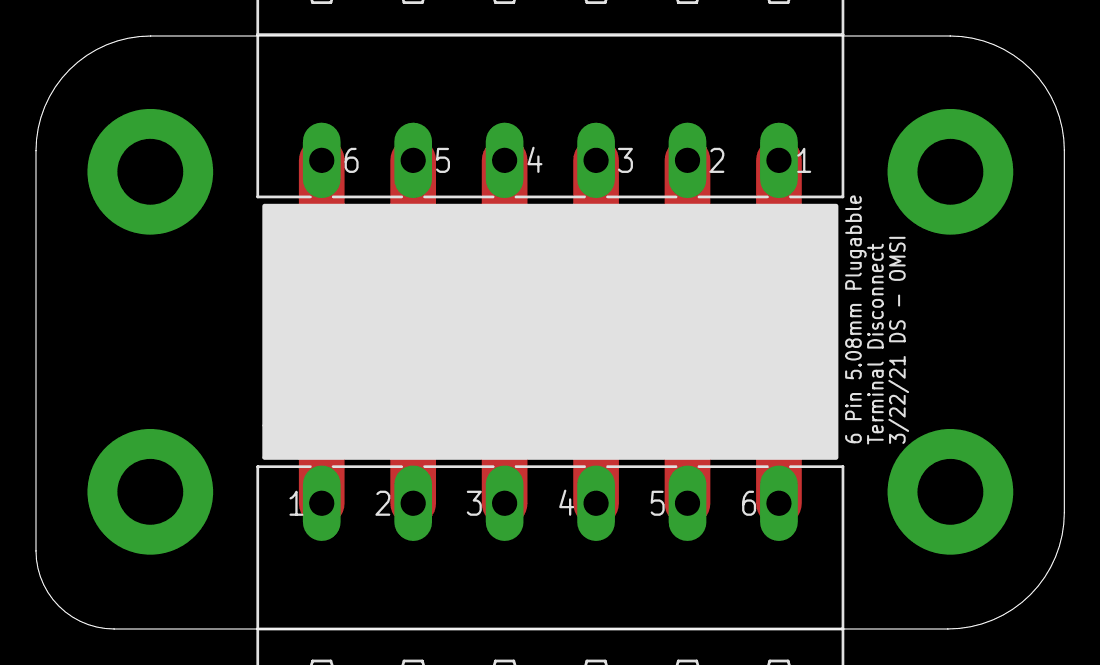
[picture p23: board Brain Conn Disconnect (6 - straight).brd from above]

Board: 2 copper layers, 57.1 x 32.9 mm, 6 parts (0 on the bottom side), 6 nets.

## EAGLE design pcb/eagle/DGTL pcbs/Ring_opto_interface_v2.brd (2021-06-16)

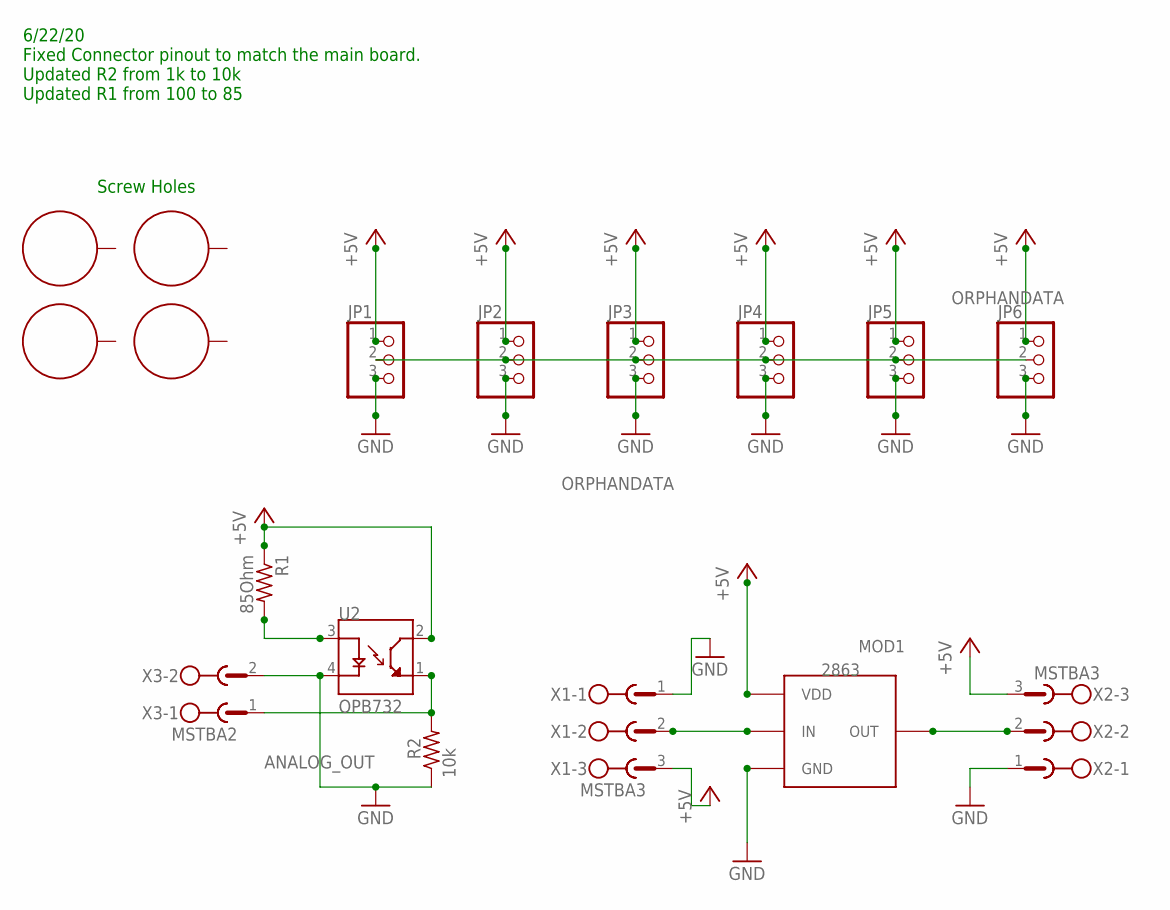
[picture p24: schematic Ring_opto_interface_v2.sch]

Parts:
H1, H2, H3, H4: STANDOFF_ELECTRICAL5-32; STANDOFF_ELECTRICAL_5_32
JP1, JP2, JP3, JP4, JP5, JP6: PINHD-1X3CB; 1X03-CLEANBIG
MOD1: 2863; ADAFRUIT_2863
R1: 85Ohm; RESAD1176W63L850D250B
R2: 10k; RESAD1176W63L850D250B
U2: OPB732; OPTO_OPB732
X1, X2: MSTBA3
X3: MSTBA2

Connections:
+5V: JP1.1, JP2.1, JP3.1, JP4.1, JP5.1, JP6.1, MOD1.VDD1 (VDD), MOD1.VDD2 (VDD), R1.1, U2.2 (CT), X1.3, X2.3
ANALOG_OUT: R2.2, U2.1 (ET), X3.1
GND: JP1.3, JP2.3, JP3.3, JP4.3, JP5.3, JP6.3, MOD1.GND1 (GND), MOD1.GND2 (GND), R2.1, U2.4 (C), X1.1, X2.1, X3.2
unnamed: R1.2, U2.3 (A)
unnamed: MOD1.IN, X1.2
unnamed: MOD1.OUT, X2.2
ORPHANDATA: JP1.2, JP2.2, JP3.2, JP4.2, JP5.2, JP6.2

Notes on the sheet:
Screw Holes
6/22/20 Fixed Connector pinout to match the main board. Updated R2 from 1k to 10k Updated R1 from 100 to 85

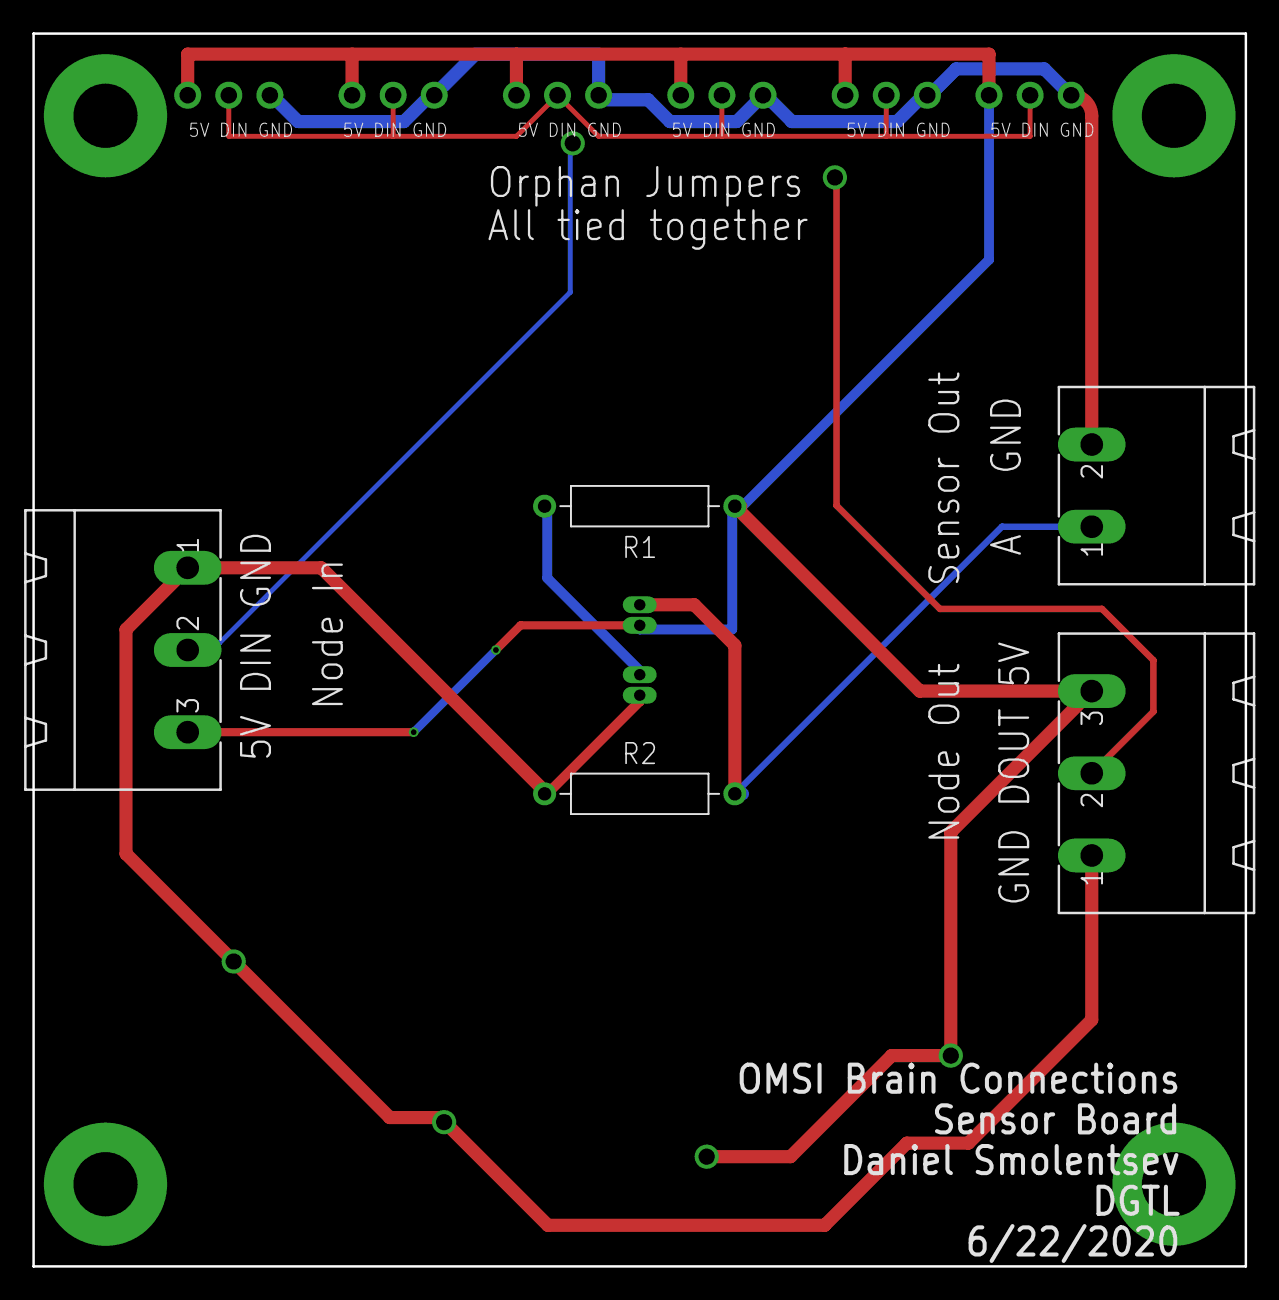
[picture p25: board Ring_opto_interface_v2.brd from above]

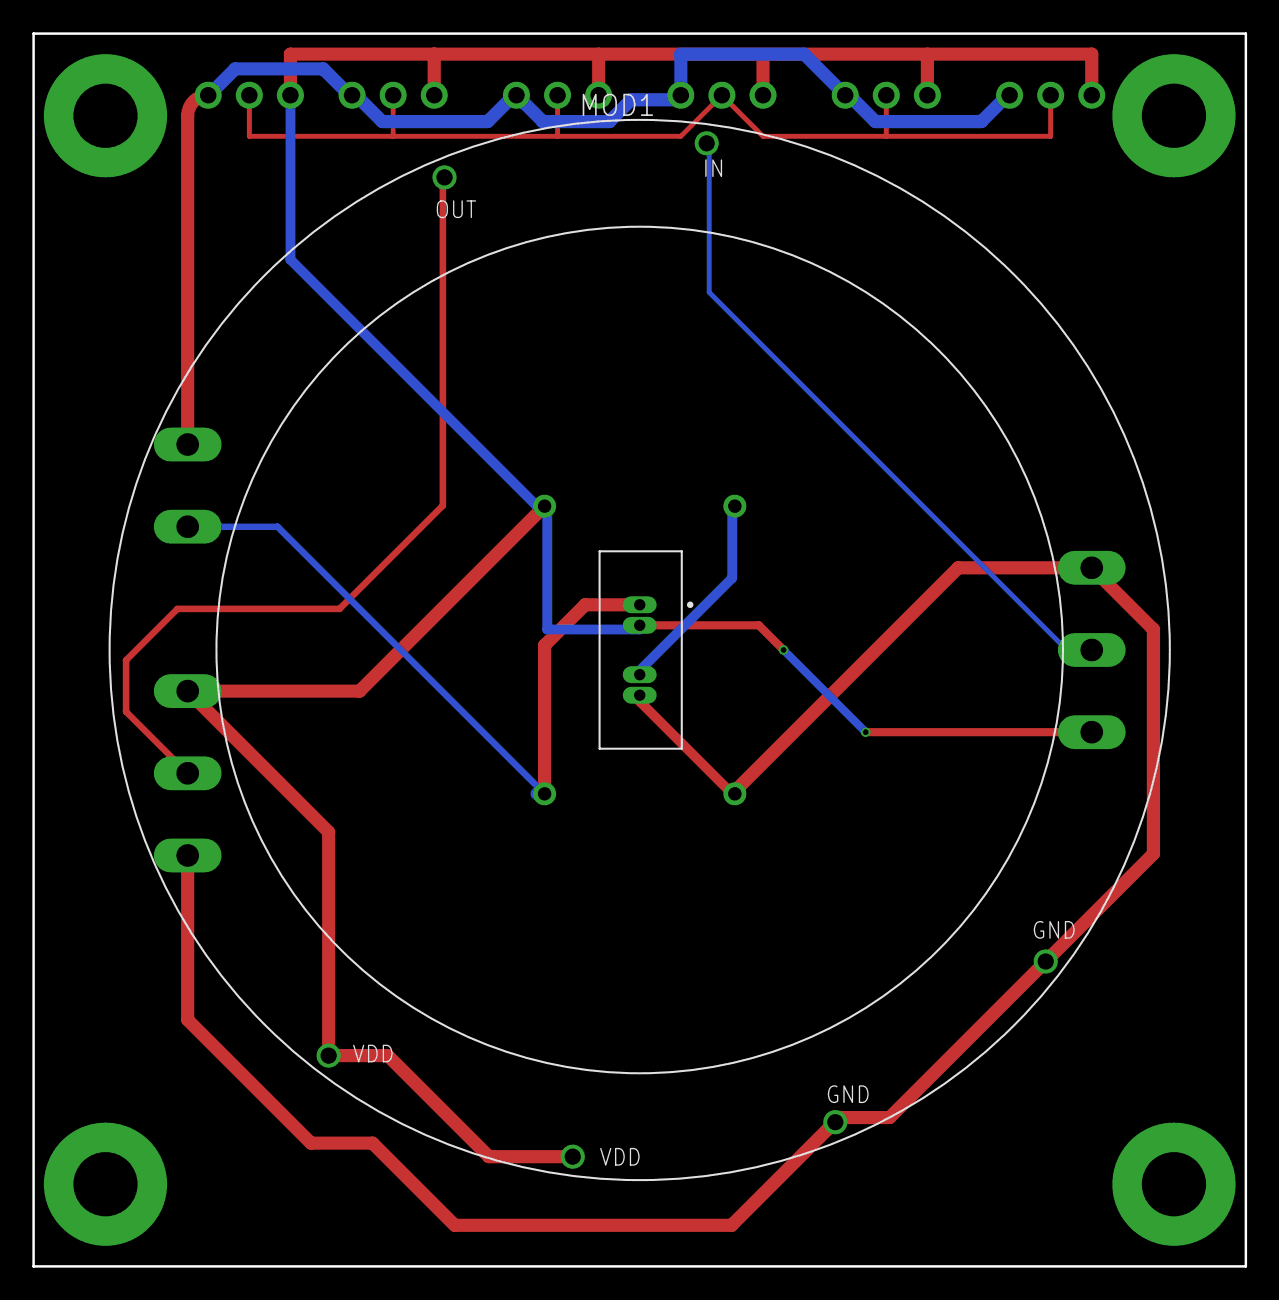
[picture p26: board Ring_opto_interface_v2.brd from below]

Board: 2 copper layers, 74.9 x 76.2 mm, 17 parts (2 on the bottom side), 7 nets.

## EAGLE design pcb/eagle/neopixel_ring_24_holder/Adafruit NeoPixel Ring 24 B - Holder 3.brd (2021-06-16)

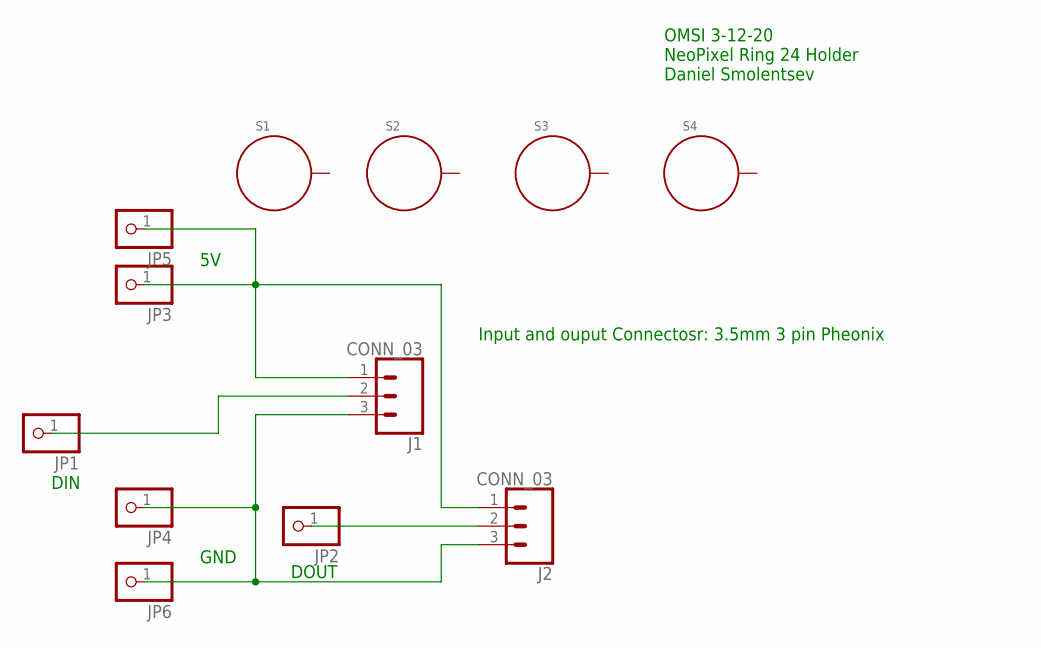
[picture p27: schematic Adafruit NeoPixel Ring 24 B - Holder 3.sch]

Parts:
J1, J2: CONN_03; 1X03_3.5MM_RA
JP1, JP2, JP3, JP4, JP5, JP6: PINHD-1X1CB; 1X01-CLEANBIG
S1, S2, S3, S4: STANDOFF_ELECTRICAL.17"; STANDOFF-ELECTRICAL

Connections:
unnamed: J1.1, J2.1, JP3.1, JP5.1
unnamed: J1.3, J2.3, JP4.1, JP6.1
unnamed: J1.2, JP1.1
unnamed: J2.2, JP2.1

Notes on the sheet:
GND
DIN
DOUT
Input and ouput Connectosr: 3.5mm 3 pin Pheonix
OMSI 3-12-20 NeoPixel Ring 24 Holder Daniel Smolentsev


Board: 2 copper layers, 82.0 x 82.2 mm, 12 parts (0 on the bottom side), 4 nets.

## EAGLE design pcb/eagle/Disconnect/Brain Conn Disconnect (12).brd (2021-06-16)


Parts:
S1, S2, S3, S4: STANDOFF_ELECTRICAL144; STANDOFF_ELECTRICAL_144MILL_NORMAL_SCREW
X5, X6: MSTBA12

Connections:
unnamed: X5.1, X6.1
unnamed: X5.2, X6.2
unnamed: X5.3, X6.3
unnamed: X5.4, X6.4
unnamed: X5.5, X6.5
unnamed: X5.6, X6.6
unnamed: X5.7, X6.7
unnamed: X5.8, X6.8
unnamed: X5.9, X6.9
unnamed: X5.10, X6.10
unnamed: X5.11, X6.11
unnamed: X5.12, X6.12


Board: 2 copper layers, 88.9 x 44.1 mm, 6 parts (0 on the bottom side), 12 nets.

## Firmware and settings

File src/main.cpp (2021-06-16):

#include <avr/pgmspace.h>
#include <Adafruit_NeoPixel.h>
#include <Wire.h>
#include <SparkFun_ADXL345.h>
//#include <MemoryFree.h>; // use this lib and freeMemory() to check for free memory

// comment out DEBUG_PRINTS to remove print statements from final build
//#define DEBUG_PRINTS

const int NODEPIN = 7;  // pin 7 is nodes line
const int NODELEDS = 168; //168; //total node pixels 
const int CONNPIN = 13;  // pin 13 is connections line
const int CONNLEDS = 188; //total connection pixels
const int ORPHANPIN = 5;  // pin 5 is orphan line
const int ORPHANLEDS = 78; //total orphan pixels
const int STATUSPIN = MISO;  // pin 14/miso is STATUS line output
const int STATUSLEDS = 8; // 3 OPTO sensors and one ADXL status indicatior, adjust for full size table

const byte fadeTable[]PROGMEM = {200, 100, 50, 15, 5, 0, 0, 0, 0, 0, 0, 0, 0, 0, 0, 0, 0, 0, 0, 0, 0, 0, 0}; // need at least as many bytes as longest connection or orphans

int rampFillOne = 255; //conn fadeup controller
int rampFillTwo = 255;
int rampFillThree = 255;
int rampFillFour = 255;
int rampFillFive = 255;
int rampFillSix = 255;
int rampFillSeven = 255;
int rampFillEight = 255;
int rampFillNine = 255;
int rampFillTen = 255;
int rampFillEleven = 255;
int rampFillTwelve = 255;

int rampFillOneWhite = 255;
int rampFillTwoWhite = 255;
int rampFillThreeWhite = 255;
int rampFillFourWhite = 255;
int rampFillFiveWhite = 255;
int rampFillSixWhite = 255;
int rampFillSevenWhite = 255;
int rampFillEightWhite = 255;
int rampFillNineWhite = 255;
int rampFillTenWhite = 255;
int rampFillElevenWhite = 255;
int rampFillTwelveWhite = 255;

//----------------------------FUNCTION PROTOTYPES FOR COMPILER----------------------------------
void setAllNodes(byte red, byte green, byte blue, byte white);
void setAllConns(byte red, byte green, byte blue, byte white);
void connTwinkle(byte red, byte green, byte blue, int SparkleDelay, int SpeedDelay);
void orphanTwinkle(byte red, byte green, byte blue, int SparkleDelay, int SpeedDelay);
void setAllOrphans(byte red, byte green, byte blue, byte white);
void winAnimation();
void pickANode(bool node1, bool node2, bool node3, bool node4, bool node5, bool node6, bool node7);  //add more nodes and dupe full function
void pickAConn(bool conn1, bool conn2, bool conn3, bool conn4, bool conn5, bool conn6, bool conn7);  //control for connection lighting
void pickAOrphan(bool node1, bool node2, bool node3, bool node4, bool node5, bool node6, bool node7); //orphan control when node is lit
void lowPulseNodes(); //Low node fade control
void highPulseNodes(); //active connection with two nodes fade control
void setStatus(bool opto1, bool opto2, bool opto3, bool opto4, bool opto5, bool opto6, bool opto7, bool adxl1); //Status output indicator
void resetNodeTimers();

//-----------------------------TILT SENSOR SETUP-------------------------------------------------
// The sensor is ADXL343, but it works with the ADXL345 library
ADXL345 adxl = ADXL345();            // USE FOR I2C COMMUNICATION
//const float ADXLTriggerValue = 265; //ADXL z axis trigger value.
int changeInAccelZ = 0;
int currentAccelZ = 0;
int accelZTriggerValue = 14; // was 20, 7 was having false triggers and staying active indefinitely.
int previousAccelZ = 0;
// FIX IDEA: use the proximity sensors to trigger a start

//---------------------------AUDIO OUT PINS FOR TRIGGERS--------------------------------------
const int Audio_1 = 8; // Attractor Song - hold level high to loop
const int Audio_2 = 12; // Start sound on 10 - edge triggered 
const int Audio_3 = 11; // Connection / Node sound on 9 - edge triggered
const int Audio_4 = 10; // Win sound on 8 - edge triggered


//--------------------------ANALOG SETUP FOR OPTOs---------------------------------------

const int node1Sensor = A6; //pin D4 is also A6
const int node2Sensor = A5;
const int node3Sensor = A3;
const int node4Sensor = A2;
const int node5Sensor = A1;
const int node6Sensor = A0;
const int node7Sensor = A4;

const int optoTriggerValue = 350;  //OPTO input level trigger values - adjust as needed
const int opto1TriggerValue = 350; //Individual OPTO values
const int opto2TriggerValue = 350; 
const int opto3TriggerValue = 350;
const int opto4TriggerValue = 350; 
const int opto5TriggerValue = 350; 
const int opto6TriggerValue = 350;
const int opto7TriggerValue = 350; 



int node1SensorValue = 0;
int node2SensorValue = 0;
int node3SensorValue = 0;
int node4SensorValue = 0;
int node5SensorValue = 0;
int node6SensorValue = 0;
int node7SensorValue = 0;

int node1OutputValue = 0;
int node2OutputValue = 0;
int node3OutputValue = 0;
int node4OutputValue = 0;
int node5OutputValue = 0;
int node6OutputValue = 0;
int node7OutputValue = 0;

//------------------------------------------SET UP NEO STRAND SEGMENTS PER GROUP---------------------------------------
const int node1LedCount = 24; // adjust if you use different sized neo rings
const int node2LedCount = 24;
const int node3LedCount = 24;
const int node4LedCount = 24;
const int node5LedCount = 24;
const int node6LedCount = 24;
const int node7LedCount = 24;

bool node1on = LOW; //use node states for game logic
bool node2on = LOW;
bool node3on = LOW;
bool node4on = LOW;
bool node5on = LOW;
bool node6on = LOW;
bool node7on = LOW;

const int conn1LedCount = 17; // adjust if you use different counts per connection groups
const int conn2LedCount = 8;
const int conn3LedCount = 23;
const int conn4LedCount = 23;
const int conn5LedCount = 8;
const int conn6LedCount = 17;
const int conn7LedCount = 17;
const int conn8LedCount = 10;
const int conn9LedCount = 16;
const int conn10LedCount = 21;
const int conn11LedCount = 16;
const int conn12LedCount = 10;


const int orphan1LedCount = 15;  // USE Longest orphan per node since they are in parallel groups
const int orphan2LedCount = 12;
const int orphan3LedCount = 10;
const int orphan4LedCount = 19;
const int orphan5LedCount = 10;
const int orphan6LedCount = 12;


Adafruit_NeoPixel node = Adafruit_NeoPixel(NODELEDS, NODEPIN, NEO_GRBW + NEO_KHZ800);
Adafruit_NeoPixel conn = Adafruit_NeoPixel(CONNLEDS, CONNPIN, NEO_GRBW + NEO_KHZ800);
Adafruit_NeoPixel orphans = Adafruit_NeoPixel(ORPHANLEDS, ORPHANPIN, NEO_GRBW + NEO_KHZ800);
Adafruit_NeoPixel sensorStatus = Adafruit_NeoPixel(STATUSLEDS, STATUSPIN, NEO_GRB + NEO_KHZ800);

//----------------------STATE MACHINE SETUP--------------------------------
enum State_enum {IDLEMODE, STARTMODE, GAMEMODE, WINMODE};
uint8_t state = WINMODE;

enum Fade_enum {FADEUP, FADEDOWN};
uint8_t fadeState = FADEUP;

enum HighFade_enum {FADEUPNODE, FADEDOWNNODE};
uint8_t highfadeState = FADEDOWNNODE;

unsigned long previousMillis = 0; // restart machine every 49 days or this might overflow!!!!!!!
const long interval = 45000; // Milliseconds before auto reset if no children are 'using' machine

const long nodeInterval = 10000; // 10 sec times for node repeat
unsigned long node1Millis = 1; // 0.001 second for start of game
unsigned long node2Millis = 1;
unsigned long node3Millis = 1;
unsigned long node4Millis = 1;
unsigned long node5Millis = 1;
unsigned long node6Millis = 1;
unsigned long node7Millis = 1;


int lowFade = 0;
int highFadeNode = 250;

bool s1, s2, s3, s4, s5, s6, s7, sADXL; //temps for sensor states
int previousS1, previousS2, previousS3, previousS4, previousS5, previousS6, previousS7;
int currentS1, currentS2, currentS3, currentS4, currentS5, currentS6, currentS7;
//float previousADXL;
//float currentADXL;

//-------------------------SETUP------------------------------------------------
void setup() {

  Serial.begin(115200); // UNCOMMENT for testing OPTO732s if needed
  /* Initialise the sensor */
  //while (!Serial) ;

  adxl.powerOn();
  adxl.setRangeSetting(2);  // Set it for 2G. 2G 4G 8G and 16G available
  Serial.print(F("ADXL started"));
  pinMode(Audio_1, OUTPUT);
  pinMode(Audio_2, OUTPUT);
  pinMode(Audio_3, OUTPUT);
  pinMode(Audio_4, OUTPUT); //not really used due to same SFX for node/conn

  node.begin(); // Initialize all pixels to 'off' states
  node.show();
  conn.begin();
  conn.show();
  orphans.begin();
  orphans.show();
  sensorStatus.begin();
  sensorStatus.show();
  delay(2000);

  //Serial.println(F("Free RAM = ")); //F function does the same and is now a built in library, in IDE > 1.0.0
  //Serial.println(freeMemory(), DEC);  // print how much RAM is available.
}

//------------------------------MAIN LOOP---------------------------------------
void loop() {
  Serial.print(F("looping"));

  unsigned long currentMillis = millis();//for 30 second reset timer function and node sound repeating

  int accelX, accelY, accelZ;
  // Read the accelerometer values and store them in variables declared above x,y,z
  adxl.readAccel(&accelX, &accelY, &accelZ);
  
  changeInAccelZ = abs(accelZ - previousAccelZ);
  currentAccelZ = accelZ;
  previousAccelZ = accelZ; // wont use previousAccelZ the rest of this loop
  
  

  // read OPTO analog values
  node1SensorValue = analogRead(node1Sensor); //Add additional sensors as needed
  node2SensorValue = analogRead(node2Sensor);
  node3SensorValue = analogRead(node3Sensor);
  node4SensorValue = analogRead(node4Sensor);
  node5SensorValue = analogRead(node5Sensor);
  node6SensorValue = analogRead(node6Sensor);
  node7SensorValue = analogRead(node7Sensor);

  node1OutputValue = node1SensorValue;
  node2OutputValue = node2SensorValue;
  node3OutputValue = node3SensorValue;
  node4OutputValue = node4SensorValue;
  node5OutputValue = node5SensorValue;
  node6OutputValue = node6SensorValue;
  node7OutputValue = node7SensorValue;


  //----------------------------------------------------SENSOR STATUS TESTING-----------------------------------
  currentS1 = node1SensorValue; //copy sensor data for input testing
  currentS2 = node2SensorValue;
  currentS3 = node3SensorValue;
  currentS4 = node4SensorValue;
  currentS5 = node5SensorValue;
  currentS6 = node6SensorValue;
  currentS7 = node7SensorValue;
  
  
  //Serial.println("after accelerometer read");
  if (abs(currentS1 - previousS1) > 70 || currentS1 < 45) s1 = 0; // test for OPEN noise or pull to GND
  else s1 = 1;

  if (abs(currentS2 - previousS2) > 70 || currentS2 < 45) s2 = 0;
  else s2 = 1;

  if (abs(currentS3 - previousS3) > 70 || currentS3 < 45) s3 = 0;
  else s3 = 1;

  if (abs(currentS4 - previousS4) > 70 || currentS4 < 45) s4 = 0;
  else s4 = 1;

  if (abs(currentS5 - previousS5) > 70 || currentS5 < 45) s5 = 0;
  else s5 = 1;

  if (abs(currentS6 - previousS6) > 70 || currentS6 < 45) s6 = 0;
  else s6 = 1;

  if (abs(currentS7 - previousS7) > 70 || currentS7 < 45) s7 = 0;
  else s7 = 1;
  
  if (changeInAccelZ > accelZTriggerValue) sADXL = 0; // Test for out of range AXIS Sensor
  else sADXL = 1;
  setStatus(s1, s2, s3, s4, s5, s6, s7, sADXL); // Update Sensor STATUS LEDs

  previousS1 = currentS1;  //store last sensor values for next test
  previousS2 = currentS2;
  previousS3 = currentS3;
  previousS4 = currentS4;
  previousS5 = currentS5;
  previousS6 = currentS6;
  previousS7 = currentS7;
  //previousADXL = currentADXL;

  

  //-------------------------------------------------END SENSOR STATUS TESTING-----------------------------------


  //--------------------------TESTING sensor event values, add new units enable if needed-----------------------------------------

  //Serial.print(F("X: ")); Serial.print(accelX); Serial.print(F("  "));
  //Serial.print(F("Y: ")); Serial.print(accelY); Serial.print(F("  "));
  //Serial.print(F("Z: ")); Serial.print(accelZ); Serial.print(F("  ")); Serial.println(F(""));

  #ifdef DEBUG_PRINTS
    Serial.print(F("accel X Y Z - changeInZ :: "));
    Serial.print(accelX);
    Serial.print(" . ");
    Serial.print(accelY);
    Serial.print(" . ");
    Serial.print(accelZ);
    Serial.print(" . ");
    Serial.print(changeInAccelZ);
    Serial.println(F(" . "));
    Serial.print(F("OPTO1: ")); Serial.print(node1OutputValue); Serial.print(F("  "));
    Serial.print(F("OPTO2: ")); Serial.print(node2OutputValue); Serial.print(F("  "));
    Serial.print(F("OPTO3: ")); Serial.print(node3OutputValue); Serial.print(F("  "));
    Serial.print(F("OPTO4: ")); Serial.print(node4OutputValue); Serial.print(F("  "));
    Serial.print(F("OPTO5: ")); Serial.print(node5OutputValue); Serial.print(F("  "));
    Serial.print(F("OPTO6: ")); Serial.print(node6OutputValue); Serial.print(F("  "));
    Serial.print(F("OPTO7: ")); Serial.print(node7OutputValue); Serial.print(F("  ")); 
    Serial.println(F(""));
  #endif

  
  //---------------------------------STATE MACHINE CONTROL LOOP-------------------------------------------
  //Serial.println(F("About to enter state switch "));
  switch (state)
  {

    case IDLEMODE:
      Serial.println(F("IdleMode"));

      if (changeInAccelZ > accelZTriggerValue) {
        digitalWrite(Audio_1, LOW); //Shut off Idle song  loop

        state = STARTMODE;
      } else {
        connTwinkle(0x00, 0x00, 0x60, 40, random(20, 100)); // twinkle connections and orphans
        lowPulseNodes(); setAllNodes(0, 0, lowFade, 0); node.show();
        orphanTwinkle(0x00, 0x00, 0x60, 40, random(20, 100)); // twinkle orphans
        lowPulseNodes(); setAllNodes(0, 0, lowFade, 0); node.show();    //run it twice due to random delays in twinkle patterns

        digitalWrite(Audio_1, HIGH);   //play idle sound (hold state)
      }
      break;

    case STARTMODE:
      Serial.println(F("StartMode"));
      digitalWrite(Audio_2, HIGH); //Trigger start sound
      delay(10);
      digitalWrite(Audio_2, LOW);
      previousMillis = currentMillis;// start 30 sec counter for bored kids
      setAllConns(0, 0, 0, 0); //reset all LEDs to off
      lowPulseNodes(); setAllNodes(0, 0, lowFade, 0); node.show();
      setAllOrphans(0, 0, 0, 0);
      state = GAMEMODE;
      highFadeNode = 250; // reset
      rampFillOne = 255; // Connection ramp controller reset
      rampFillTwo = 255; // Connection ramp controller reset
      rampFillThree = 255;
      rampFillFour = 255;
      rampFillFive = 255;
      rampFillSix = 255;
      rampFillSeven = 255;
      rampFillEight = 255;
      rampFillNine = 255;
      rampFillTen = 255;
      rampFillEleven = 255;
      rampFillTwelve = 255;

      rampFillOneWhite = 255;
      rampFillTwoWhite = 255;
      rampFillThreeWhite = 255;
      rampFillFourWhite = 255;
      rampFillFiveWhite = 255;
      rampFillSixWhite = 255;
      rampFillSevenWhite = 255;
      rampFillEightWhite = 255;
      rampFillNineWhite = 255;
      rampFillTenWhite = 255;
      rampFillElevenWhite = 255;
      rampFillTwelveWhite = 255;


      break;

    case GAMEMODE:
      Serial.println(F("GAMEMODE"));

      if (changeInAccelZ > accelZTriggerValue) previousMillis = currentMillis;// reset inactivity timeout if movement
      if (node1OutputValue > opto1TriggerValue & currentMillis - node1Millis >= nodeInterval) { //Node 1 interaction test
        digitalWrite(Audio_3, HIGH);
        delay(10);
        digitalWrite(Audio_3, LOW);
        node1on = 1;
        node1Millis = currentMillis;
        previousMillis = currentMillis; // reset inactivity timeout
      }
      if (node2OutputValue > opto2TriggerValue & currentMillis - node2Millis >= nodeInterval) { //Node 2 interaction test
        digitalWrite(Audio_3, HIGH);
        delay(10);
        digitalWrite(Audio_3, LOW);
        node2on = 1;
        node2Millis = currentMillis;
        previousMillis = currentMillis; // reset inactivity timeout
      }
      if (node3OutputValue > opto3TriggerValue & currentMillis - node3Millis >= nodeInterval) { //Node 3 interaction test
        digitalWrite(Audio_3, HIGH);
        delay(10);
        digitalWrite(Audio_3, LOW);
        node3on = 1;
        node3Millis = currentMillis;
        previousMillis = currentMillis; // reset inactivity timeout
      }
      if (node4OutputValue > opto4TriggerValue & currentMillis - node4Millis >= nodeInterval) { //Node 4 interaction test
        digitalWrite(Audio_3, HIGH);
        delay(10);
        digitalWrite(Audio_3, LOW);
        node4on = 1;
        node4Millis = currentMillis;
        previousMillis = currentMillis; // reset inactivity timeout
      }
      if (node5OutputValue > opto5TriggerValue & currentMillis - node5Millis >= nodeInterval) { //Node 5 interaction test
        digitalWrite(Audio_3, HIGH);
        delay(10);
        digitalWrite(Audio_3, LOW);
        node5on = 1;
        node5Millis = currentMillis;
        previousMillis = currentMillis; // reset inactivity timeout
      }
      if (node6OutputValue > opto6TriggerValue & currentMillis - node6Millis >= nodeInterval) { //Node 6 interaction test
        digitalWrite(Audio_3, HIGH);
        delay(10);
        digitalWrite(Audio_3, LOW);
        node6on = 1;
        node6Millis = currentMillis;
        previousMillis = currentMillis; // reset inactivity timeout
      }
      if (node7OutputValue > opto7TriggerValue & currentMillis - node7Millis >= nodeInterval) { //Node 7 interaction test
        digitalWrite(Audio_3, HIGH);
        delay(10);
        digitalWrite(Audio_3, LOW);
        node7on = 1;
        node7Millis = currentMillis;
        previousMillis = currentMillis; // reset inactivity timeout
      }

//----------------------------------------------------------------------------------------------
//--------------------------------Serial Input for Testing -------------------------------------
//----------------------------------------------------------------------------------------------
// Uncomment to test node on states from Serial input
/*
      while(Serial.available() > 0) {

        int num = Serial.parseInt();
        switch(num) {
          case 1:
          node1on = 1;
          break;
          case 2:
          node2on = 1;
          break;
          case 3:
          node3on = 1;
          break;
          case 4:
          node4on = 1;
          break;
          case 5:
          node5on = 1;
          break;
          case 6:
          node6on = 1;
          break;
          case 7:
          node7on = 1;
          break;
          default:
          Serial.println(F("node num out of bounds"));
        }
      }
      Serial.print(F("Node1on: ")); Serial.print(node1on); Serial.print(F(" ,Node2on")); Serial.print(node2on); Serial.print(F(" ,Node3on: ")); Serial.print(node3on);
      Serial.print(F(" ,Node4on: ")); Serial.print(node4on); Serial.print(F(" ,Node5on: ")); Serial.print(node5on); Serial.print(F(" ,Node6on: ")); Serial.print(node6on);
      Serial.print(F(" ,Node7on: ")); Serial.print(node7on); Serial.println(F(""));
*/
      pickANode(node1on, node2on, node3on, node4on, node5on, node6on, node7on); // Light up nodes
      pickAConn(node1on, node2on, node3on, node4on, node5on, node6on, node7on); // Light up connections
      pickAOrphan(node1on, node2on, node3on, node4on, node5on, node6on, node7on); // Light up orphans

      if (currentMillis - previousMillis >= interval) {
        setAllConns(0, 0, 0, 0); setAllNodes(0, 0, 0, 0); setAllOrphans(0, 0, 0, 0); // reset playfield
        node1on = 0, node2on = 0, node3on = 0, node4on = 0, node5on = 0, node6on = 0, node7on = 0; // reset node state,  expand for full project
        state = IDLEMODE; //Back to Idle if no movement
      }
      if (node1on == 1 & node2on == 1 & node3on == 1 & node4on == 1 & node5on == 1 & node6on == 1 & node7on == 1) state = WINMODE;

      
      break;

    case WINMODE: 
      Serial.println(F("winmode!"));
      digitalWrite(Audio_4, HIGH);
      delay(10);
      digitalWrite(Audio_4, LOW);
      previousMillis = currentMillis; // reset for win animation
      resetNodeTimers();
      setStatus(1, 1, 1, 1, 1, 1, 1, 1); // green on all STATUS indicators, test the indicator LED test....
      //Serial.println(F("Free RAM  from winmode= ")); 
      //Serial.println(freeMemory(), DEC);  // print how much RAM is available.
      /*
      int loopCount = 0;
      do {
        pickANode(node1on, node2on, node3on, node4on, node5on, node6on, node7on); // Light up nodes while end animation
        pickAConn(node1on, node2on, node3on, node4on, node5on, node6on, node7on); // Light up connections
        pickAOrphan(node1on, node2on, node3on, node4on, node5on, node6on, node7on); // Light up orphans
        loopCount++;
      } while (loopCount <= 16); // do more sparkle before fade
      */
      setAllConns(0, 0, 0, 0); setAllNodes(0, 0, 0, 0); setAllOrphans(0, 0, 0, 0); // reset playfield
      node1on = 0, node2on = 0, node3on = 0, node4on = 0, node5on = 0, node6on = 0, node7on = 0; // reset node state
      
      winAnimation();
      setAllConns(0, 0, 0, 0); setAllNodes(0, 0, 0, 0); setAllOrphans(0, 0, 0, 0); // reset playfield
      delay(1000); // pause befor reset to idle
      state = IDLEMODE;
    
      break;
  }

}

//----------------------------------------------------------------------------------------------
//---------------------------------LIGHTING FUNCTIONS BELOW-------------------------------------
//----------------------------------------------------------------------------------------------


//---------------------------------CONNECTION-TWINKLE FUNCTION----------------------------------

void connTwinkle(byte red, byte green, byte blue, int SparkleDelay, int SpeedDelay) {
  setAllConns(red, green, blue, 0);

  int Pixel = random(CONNLEDS);
  conn.setPixelColor(Pixel, conn.Color(0x00, 0x00, 0xff, 0xff)); //full blue and white for star effect
  conn.show();
  delay(SparkleDelay);
  conn.setPixelColor(Pixel, conn.Color(red, green, blue, 0x00)); //add other colors
  conn.show();
  delay(SpeedDelay);

  //Serial.println(F("Free RAM from conn twinkler = ")); 
  //Serial.println(freeMemory(), DEC);  // print how much RAM is available.
}

//---------------------------------ORPHAN-TWINKLE FUNCTION-------------------------------------
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

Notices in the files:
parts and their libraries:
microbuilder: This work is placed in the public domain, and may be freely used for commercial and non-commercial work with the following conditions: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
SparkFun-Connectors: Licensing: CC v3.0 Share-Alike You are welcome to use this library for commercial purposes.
